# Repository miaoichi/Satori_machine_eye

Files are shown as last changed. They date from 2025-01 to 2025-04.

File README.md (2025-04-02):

# 機械覺之瞳

## 本專案基於 GPL3.0 開源協議，任何基於該專案的修改和衍生作品均需開源，且必須使用相同的 GPL3.0 協議！無良抄襲禁止！

## 作者
覺瞳模型：牧之原鈴華

攝影機瞳孔件：早睡（b站 鯊鯊製造）

PCB板：R餅銳度不夠

軟體：Cirnocon

fumo辨識：Yuan xu

覺之瞳計畫交流群 qq：727559409

## 專案結構
- `3d` 覺瞳模型文件

- `esp32eye` 覺瞳軟體

- `pcb` 覺瞳 ***pcb*** 板文件

- `LICENSE.txt` 開源協議

- `README.md`

## 食用方法

克隆此項目到本地，查看每個資料夾下的 ***README.md***

3d列印就查看 ***3d*** 資料夾，電路板查看 ***pcb***資料夾，軟體部分查看 ***esp32eye*** 資料夾。

連接覺之瞳 ***WiFi***：覺之瞳（無密碼）

瀏覽器開啟網頁遙控器：http://192.168.4.1

## 注意事項
電腦端滑鼠滾輪單獨控制上眼皮

手機遙控目前不太穩定，視訊推流畫質也不能再高了，主要是 ***esp32*** 算力和 ***AsyncWebServer*** 庫的限制，不建議視頻推流和遙控同時開啟，覺瞳被設置為奔潰自動閉眼並重啟。電腦端沒啥大問題。未來可能會用 ***vue3*** 重寫。

網頁頁面寫得不是很優雅，主要是我不會寫 ***css***，願意的話可以幫我改（（

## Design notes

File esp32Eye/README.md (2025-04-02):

# 機械覺之瞳-esp32eye
## 作者
Cirnocon -> miaoichi 

## 聯絡方式
電子郵件：miaoichi@gmail.com

GitHub：https://github.com/miaoichi

## 專案結構
- `ESP32EYE/`
 - `boards` 開發板設定文件，主要是啟用psram

 - `data` SPIFFS檔案儲存資料夾
 - `index.html` html文件

 - `nipplejs.min.js` 搖桿庫

 - `lib/` 自訂庫資料夾
 - `AsyncWebCam`

 - `src/` 原始碼資料夾
 - `main.cpp`

 - `partitions.csv` 分區表

 - `platformio.ini` ***PlatformIO*** 設定檔

## 食用方法
***vscode*** 下載 ***PlatformIO IDE*** 插件

> ***左側欄拓展圖示*** -> ***搜尋 PlatformIO IDE*** -> ***安裝***

打開 ***esp32eye*** 資料夾

> ***左上角檔案*** -> ***開啟資料夾*** -> ***找到 esp32eye 資料夾***

上傳 ***SPIFFS*** 系統文件

> ***左側欄小螞蟻圖示*** -> ***Bulid Filesystem Image*** -> ***Program Size*** -> ***Upload Filesystem Image***

編譯並燒錄文件

> ***左側欄小螞蟻圖示*** -> ***Build*** -> ***Upload***

## 注意事項
所有設定檔都是基於 ***ESP32-S3-N16R8*** 寫的

***platformio*** 的程式燒錄並不會自動更新 ***SPIFFS*** 系統文件，需要手動更新

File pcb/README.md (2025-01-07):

# 机械觉之瞳-pcb
## 作者
R饼锐度不够

## 嘉立创开源网址
https://oshwhub.com/flanker-e/esp32s3-open-source-of-jue

## 注意事项
板子天线需要自己单独购买

> 仅供参考：ESP8266 ESP-WROOM-02U ESP32-WROOM-32U IPEX天线2.4G ESP32天线 https://item.taobao.com/item.htm?id=598789753202

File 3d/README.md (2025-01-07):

# 机械觉之瞳-3d
## 作者
觉之瞳模型文件：觉之瞳项目交流群 qq：727559409

ov2640摄像头件：早睡（b站 鲨鲨制造）

## 食用方法
### 如何打印
直接打印 ***'已摆盘好.3mf'*** 文件

不建议修改摆盘方式，因为有些零件（比如眼球转轴）需要竖着打印，不然装配起来就非常麻烦，逝量打磨警告

如果你打算使用摄像头的话，请额外打印 ***'ov2640摄像头件'*** 文件夹里的两个文件，并删除 ***'已摆盘好.3mf'*** 文件中的瞳孔件（如果你不在意多打印一个零件的话，可以不删）

### 购买零件
舵机: mg90s 180° 

螺丝: M3\*4 M3\*6 M2\*3 若干

杜邦线：公对母 公对公 母对母若干

摄像头: ov2640 无畸变68度 （不装摄像头可以不买）

### 如何安装
***STR-lite*** 文件夹里存放的是所有零件的模型文件。使用任意可以查看 ***.prt*** 文件的软件打开里面的 ***STR-lite.prt*** 文件。手动调整零件位置，查看内部结构，然后拼装。

### 注意事项
不同材质打印的零件会有不同程度的膨胀或收缩，逝量打磨。

***STR-lite.prt*** 文件中名为 ***rack-lite*** 的零件与上眼皮的连接是要用502粘的

螺丝可以直接用买舵机送的螺丝（你甚至可以不拧，因为零件大概率会很紧）

购买舵机的时候请注意，是180度旋转范围的，不是90也不是360！90度的范围太小，360的不能控制旋转角度！

舵机建议购买tiankongrc品牌的。

摄像头瞳孔件是按照 ***ov2640 无畸变68度*** 设计的，即使型号一样，不同度数的摄像头大小也不一样！不要买错型号！（能安进去就当我没说，不过我没试过别的型号）

安装的时候请温柔，小心断件（（

记得上润滑油/雪油，转动更加丝滑

如果你打算把某些零件粘起来，请先调整好舵机角度！

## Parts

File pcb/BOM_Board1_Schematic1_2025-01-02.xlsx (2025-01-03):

No. | Quantity | Comment | Designator | Footprint | Value | Manufacturer Part | Manufacturer | Supplier Part | Supplier
1 | 9 | 100nF | C1,C29,C32,C33,C34,C35,C36,C37,C38 | C0603 | 100nF | CL10B104KB8NNNC | SAMSUNG(三星) | C1591 | LCSC
2 | 1 | 1uF | C2 | C0603 | 1uF | CL10A105KB8NNNC | SAMSUNG(三星) | C15849 | LCSC
3 | 7 | 10u | C4,C5,C26,C39,C40,C41,C42 | C0603 | 10u
4 | 8 | 22uF | C6,C7,C8,C9,C10,C11,C30,C31 | C0805 | 22uF | CL21A226MAQNNNE | SAMSUNG(三星) | C45783 | LCSC
5 | 1 | 2.2uF | C12 | C0603 | 2.2uF | CL10A225KB8NNNC | SAMSUNG(三星) | C913904 | LCSC
6 | 1 | 4.7uF | C13 | C0603 | 4.7uF | CL10A475KO8NNNC | SAMSUNG(三星) | C19666 | LCSC
7 | 3 | 220uF | C14,C15,C16 | CAP-SMD_BD6.3-L6.6-W6.6-FD-A | 220uF | OVZ221M0JTR-0606 | lelon(立隆) | C182403 | LCSC
8 | 2 | SS14L | D1,D2 | SOD-123F_L2.8-W1.8-LS3.7-RD |  | SS14L | Hottech(合科泰) | C190475 | LCSC
9 | 1 | 12H1300C | F1 | F1206 |  | 12H1300C | LANSON(良胜) | C182445 | LCSC
10 | 1 | AFC01-S08FCA-00 | FPC2 | FPC-SMD_P0.50-8P_FGS-XJ-H2.0 |  | AFC01-S08FCA-00 | JS(钜硕电子) | C262657 | LCSC
11 | 1 | AFC24-S24FIA-00 | FPC3 | FPC-SMD_P0.50-24P_QCHF-SM-H2.0 |  | AFC24-S24FIA-00 | JS(钜硕电子) | C262683 | LCSC
12 | 4 | HDR-M_2.54_1x3P | H1,H2,H3,H4 | HDR-TH_3P-P2.54-V-M |  |  |  | C2937625
13 | 1 | 1uH | L1 | IND-SMD_L7.0-W6.6 | 1uH | FXL0630-1R0-M | cjiang(长江微电) | C167216 | LCSC
14 | 1 | 4.7uH | L2 | IND-SMD_L4.4-W4.2 | 4.7uH | FXL0420-4R7-M | cjiang(长江微电) | C167208 | LCSC
15 | 4 | NCD0603Y1 | LED1,LED2,LED3,LED4 | LED0603-RD |  | NCD0603Y1 | 国星光电 | C84268 | LCSC
16 | 2 | SS8050_C541705 | Q1,Q2 | SOT-23-3_L2.9-W1.3-P1.90-LS2.4-BR |  | SS8050 | AnBon | C541705 | LCSC
17 | 8 | 10K | R7,R8,R9,R10,R16,R17,R18,R19 | R0603 | 10K
18 | 2 | 5.1K | R11,R12 | R0603 | 5.1K
19 | 1 | 500mΩ | R13 | R0805 | 500mΩ | FRL0805JR500TS | FOJAN(富捷) | C2934281 | LCSC
20 | 1 | 2 | R14 | R0603 | 2
21 | 1 | 100 | R15 | R0603 | 100
22 | 1 | 0 | R20 | R0603 | 0
23 | 1 | ESP32-S3-WROOM-1U-N16R8 | U2 | WIRELM-SMD_ESP32-S3-WROOM-1U |  | ESP32-S3-WROOM-1U-N16R8 | ESPRESSIF(乐鑫) | C3013946 | LCSC
24 | 1 | IP3005A | U3 | ESOP-8_L4.9-W3.9-P1.27-LS6.0-BL-EP |  | IP3005A | INJOINIC(英集芯) | C181685 | LCSC
25 | 1 | IP5306 | U4 | ESOP-8_L4.9-W3.9-P1.27-LS6.0-BL-EP |  | IP5306 | INJOINIC(英集芯) | C181692 | LCSC
26 | 1 | HC-C5080-2AS | U5 | CONN-TH_HC-C5080-2AS |  | HC-C5080-2AS | HCTL(华灿天禄) | C5221225 | LCSC
27 | 1 | AP63203WU-7 | U8 | TSOT-26_L2.9-W1.6-P0.95-LS2.8-BL |  | AP63203WU-7 | DIODES(美台) | C780769 | LCSC
28 | 1 | KH-SS12F23-G6 | U10 | SW-TH_KH-SS12F23-G6 |  | KH-SS12F23-G6 | kinghelm(金航标) | C5274466 | LCSC
29 | 1 | XC6206P282MR | U11 | SOT-23-3_L2.9-W1.3-P0.95-LS2.4-BR |  | XC6206P282MR | HXY MOSFET(华轩阳电子) | C5148690 | LCSC
30 | 1 | XC6206P182MR(1uA) | U12 | SOT-23-3_L2.9-W1.6-P1.90-LS2.8-BR |  | XC6206P182MR(1uA) | TECH PUBLIC(台舟) | C2827651 | LCSC
31 | 1 | CH340C | U13 | SOP-16_L10.0-W3.9-P1.27-LS6.0-BL |  | CH340C | WCH(南京沁恒) | C84681 | LCSC
32 | 1 | KH-TYPE-C-16P | USB1 | USB-C-SMD_KH-TYPE-C-16P |  | KH-TYPE-C-16P | Shenzhen Kinghelm Elec | C709357 | LCSC

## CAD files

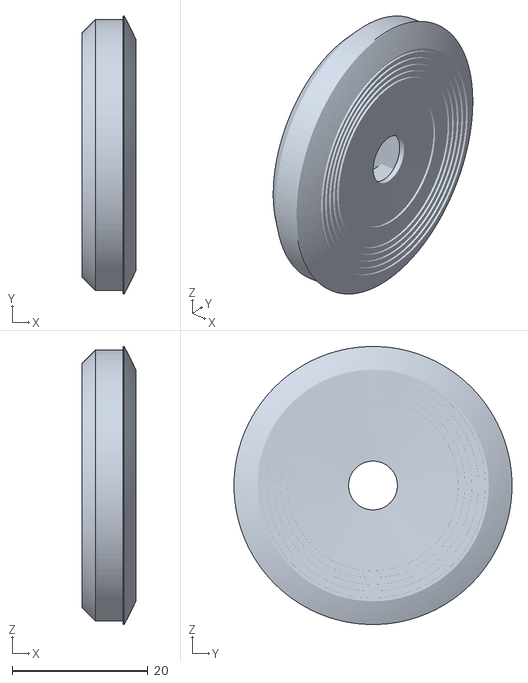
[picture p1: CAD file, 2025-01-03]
3d/ov2640摄像头件/瞳孔摄像头.stl
7.92 x 41.0 x 41.0

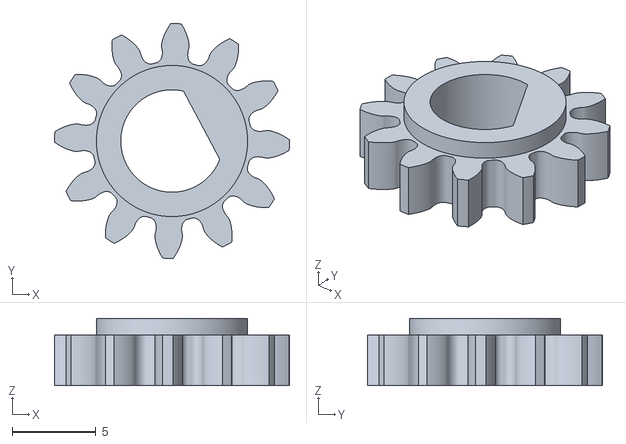
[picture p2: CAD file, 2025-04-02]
3d/stl/gear2.stl
14.0 x 14.0 x 4.00

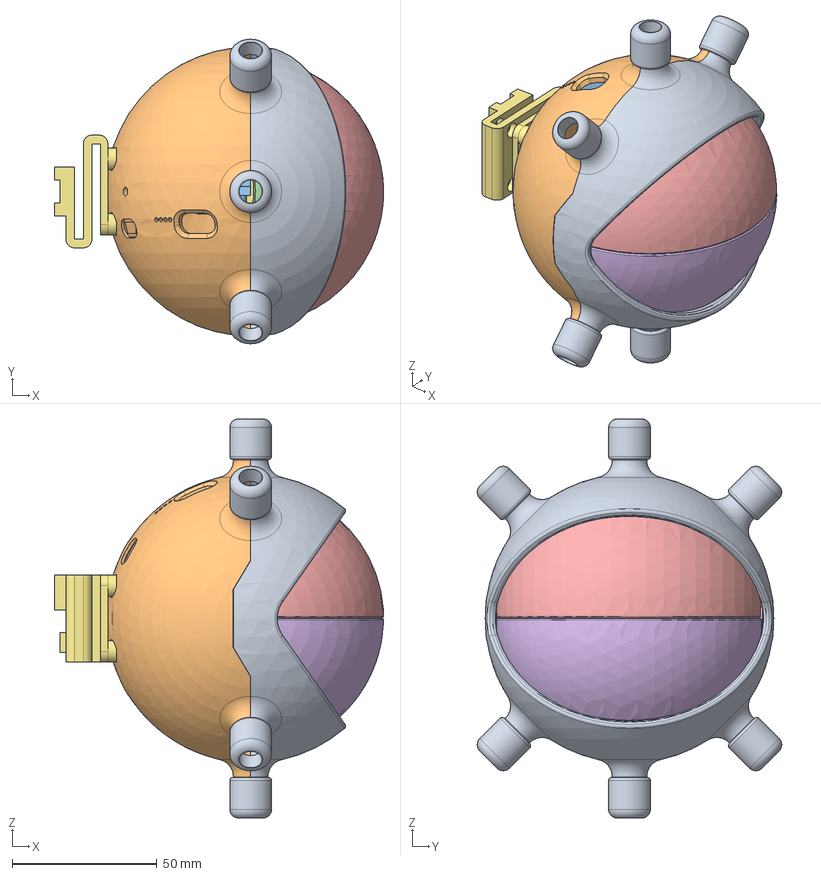
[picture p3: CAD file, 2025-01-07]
3d/STR-lite/step/STR-lite.stp
113.9 x 105.3 x 138.0 mm
MG90S x 3
servo pin
YAOBI
rocker
rack-lite
support-1
pupil
gear1
gear2

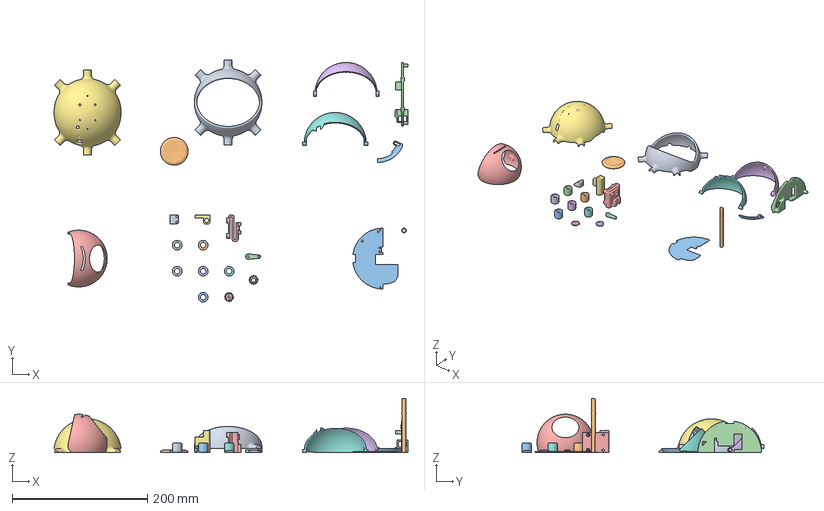
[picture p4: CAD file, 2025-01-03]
3d/已摆盘好.3mf
523.6 x 358.4 x 80.5 mm
01.stl
08.stl
pad.stl
03-1.stl
support-1.stl
06.stl
07.stl
05.stl
servo pin.stl
09.stl x 6
rack-rc.stl
04.stl
02.stl
pupil.stl
rocker.stl
gear1.stl
gear2.stl

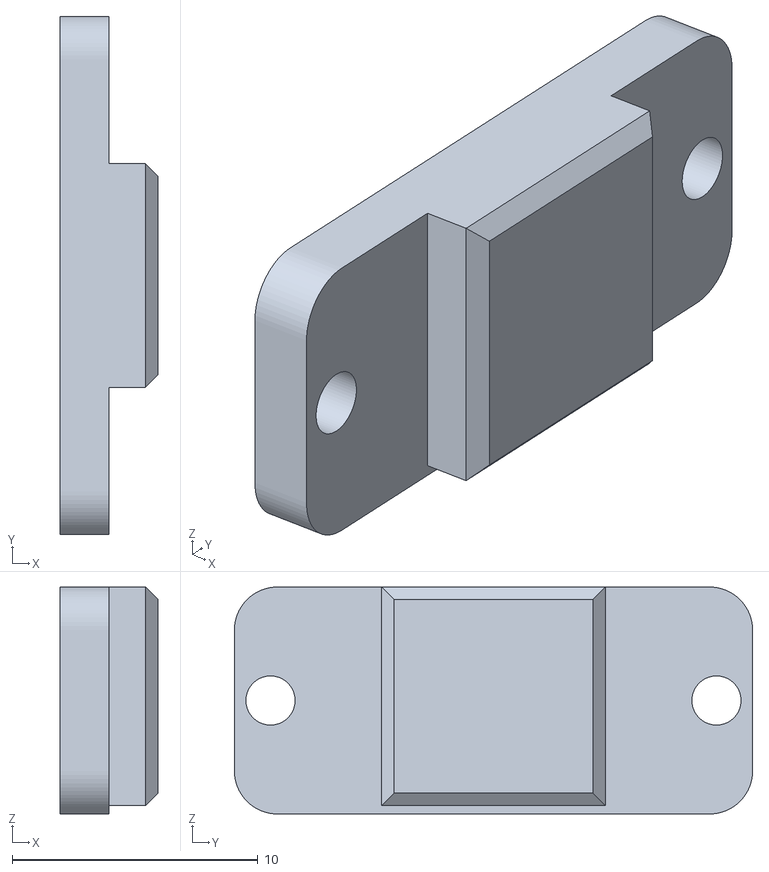
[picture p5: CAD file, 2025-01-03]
3d/ov2640摄像头件/瞳孔摄像头盖板.stl
4.00 x 21.1 x 9.24

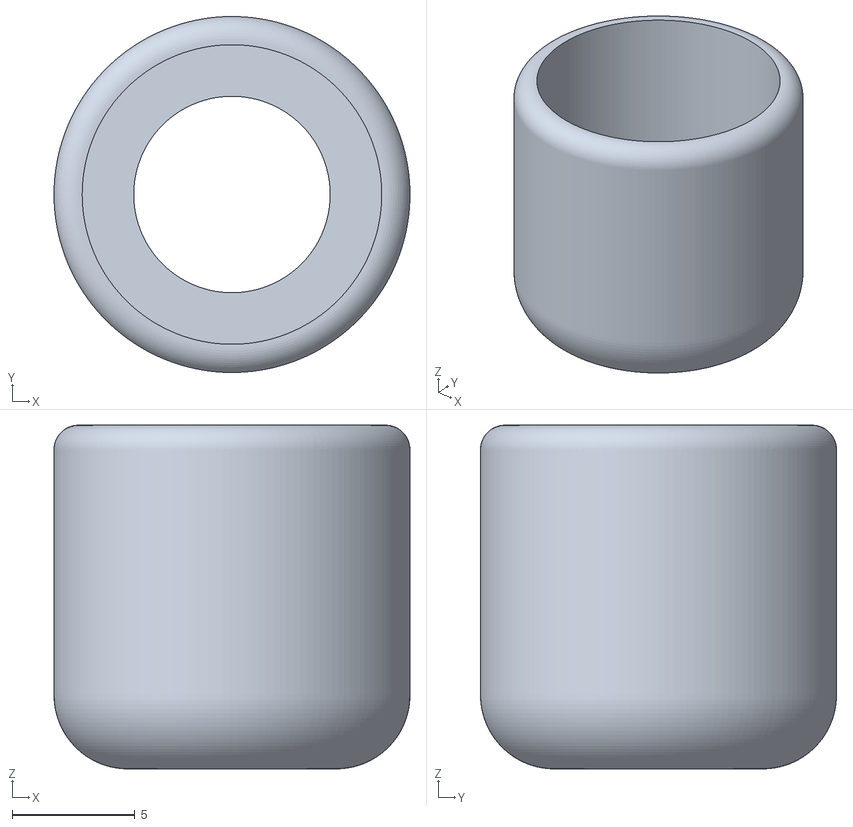
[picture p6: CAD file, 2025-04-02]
3d/stl/09.stl
14.5 x 14.5 x 14.0

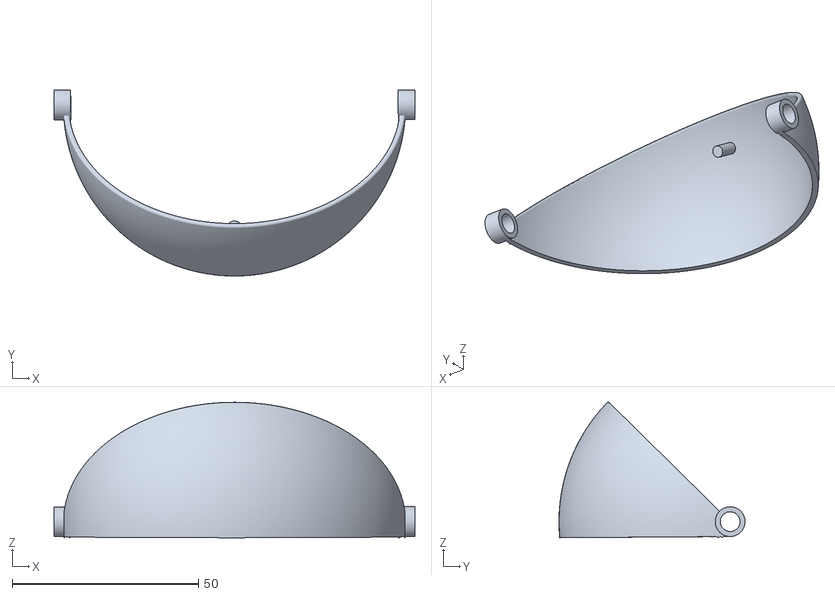
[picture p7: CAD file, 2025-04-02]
3d/stl/06.stl
97.0 x 50.0 x 36.4

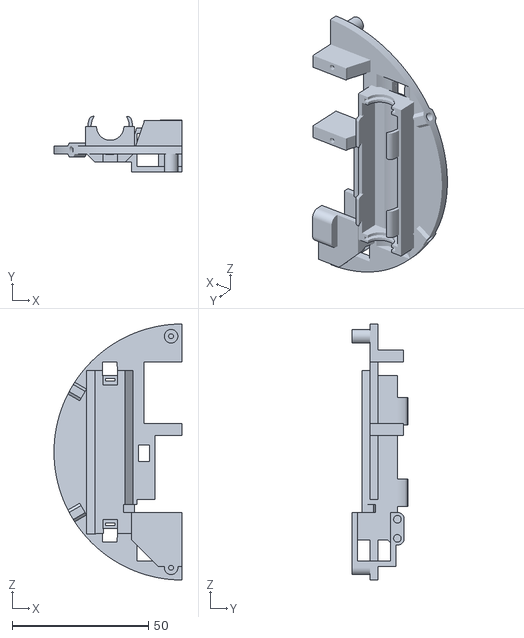
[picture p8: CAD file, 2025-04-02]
3d/stl/03-modfied1.stl.stl
47.0 x 20.4 x 94.0

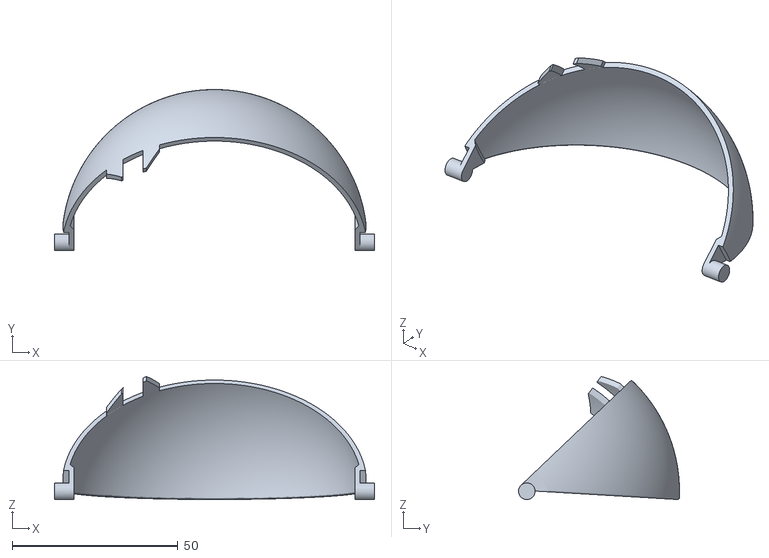
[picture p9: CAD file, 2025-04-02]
3d/stl/05.stl
96.4 x 48.5 x 37.1

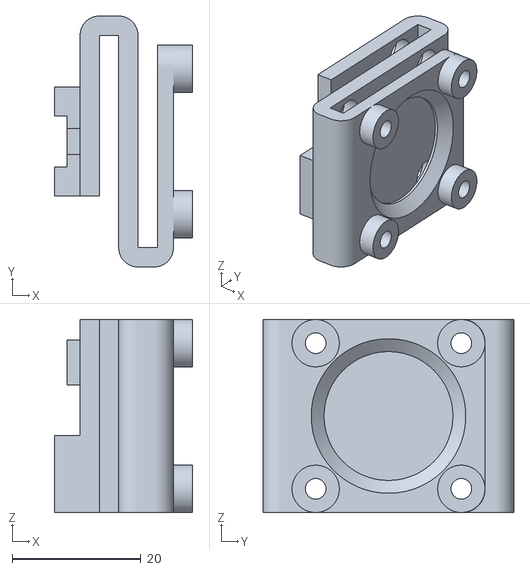
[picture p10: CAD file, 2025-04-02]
3d/stl/support-1.stl
21.5 x 39.0 x 30.0

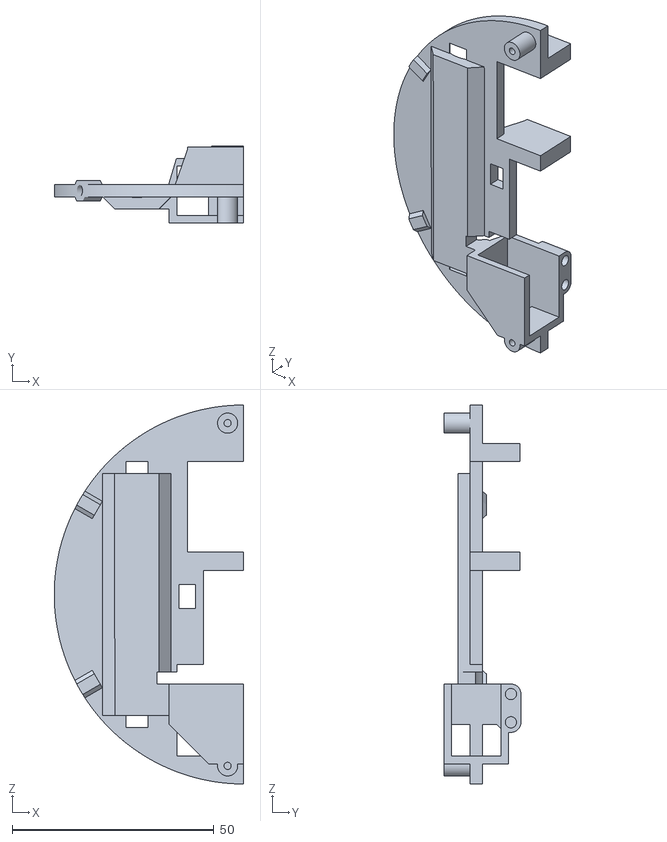
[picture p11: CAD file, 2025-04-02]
3d/stl/03-1.stl
47.0 x 19.1 x 94.0

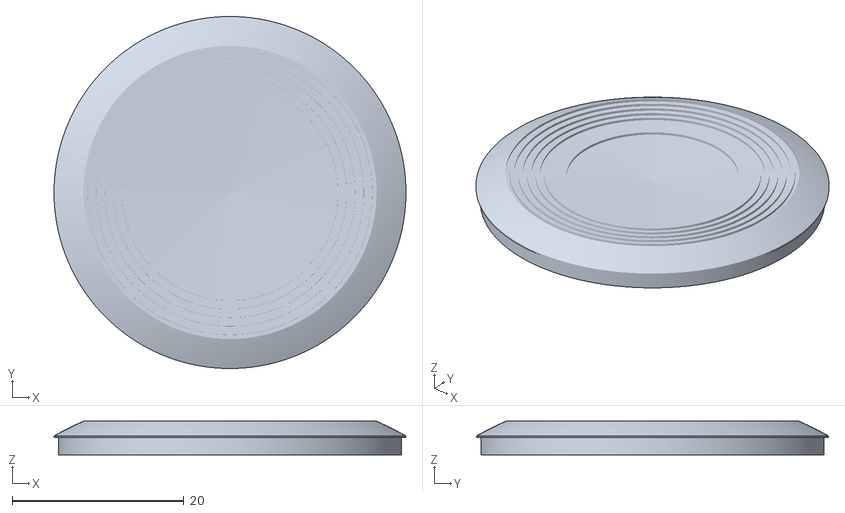
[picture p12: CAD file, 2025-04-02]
3d/stl/pupil.stl
41.0 x 41.0 x 3.92

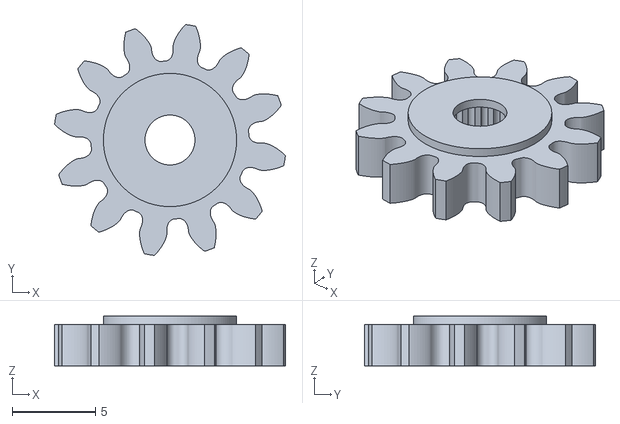
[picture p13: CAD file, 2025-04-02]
3d/stl/gear1.stl
13.9 x 13.9 x 3.00

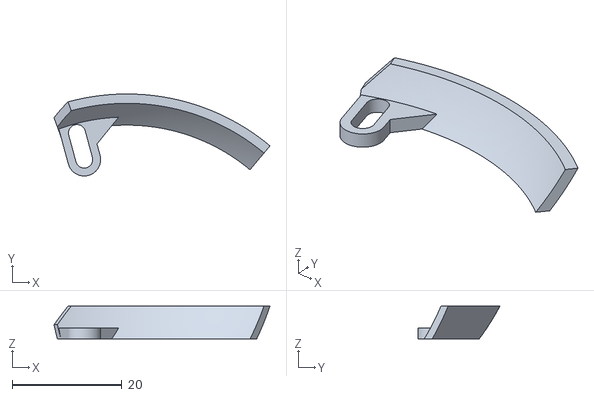
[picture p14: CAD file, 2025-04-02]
3d/stl/rack-lite.stl
39.4 x 15.0 x 6.00

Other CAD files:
3d/stl/servo pin.stl
3d/stl/07-modified.stl
3d/stl/08.stl
3d/stl/rocker.stl
3d/STR-lite/01.prt
3d/STR-lite/02.prt
3d/STR-lite/03-1.prt
3d/STR-lite/04.prt
3d/STR-lite/05.prt
3d/STR-lite/06.prt
3d/STR-lite/07.prt
3d/STR-lite/08.prt
3d/STR-lite/09.prt
3d/STR-lite/18650.prt
3d/STR-lite/MG90S.prt
3d/STR-lite/STR-lite.prt
3d/STR-lite/YAOBI.prt
3d/STR-lite/gear1.prt
3d/STR-lite/gear2.prt
3d/STR-lite/pupil.prt
3d/STR-lite/rack-lite.prt
3d/STR-lite/rocker.prt
3d/STR-lite/servo pin.prt
3d/STR-lite/support-1.prt
3d/stl/07.stl
3d/stl/09(1).stl
3d/stl/09(2).stl
3d/stl/09(3).stl
3d/stl/09(4).stl
3d/stl/09(5).stl
3d/stl/YAOBI.stl

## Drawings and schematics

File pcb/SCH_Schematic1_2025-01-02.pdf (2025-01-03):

### PW_USB5V

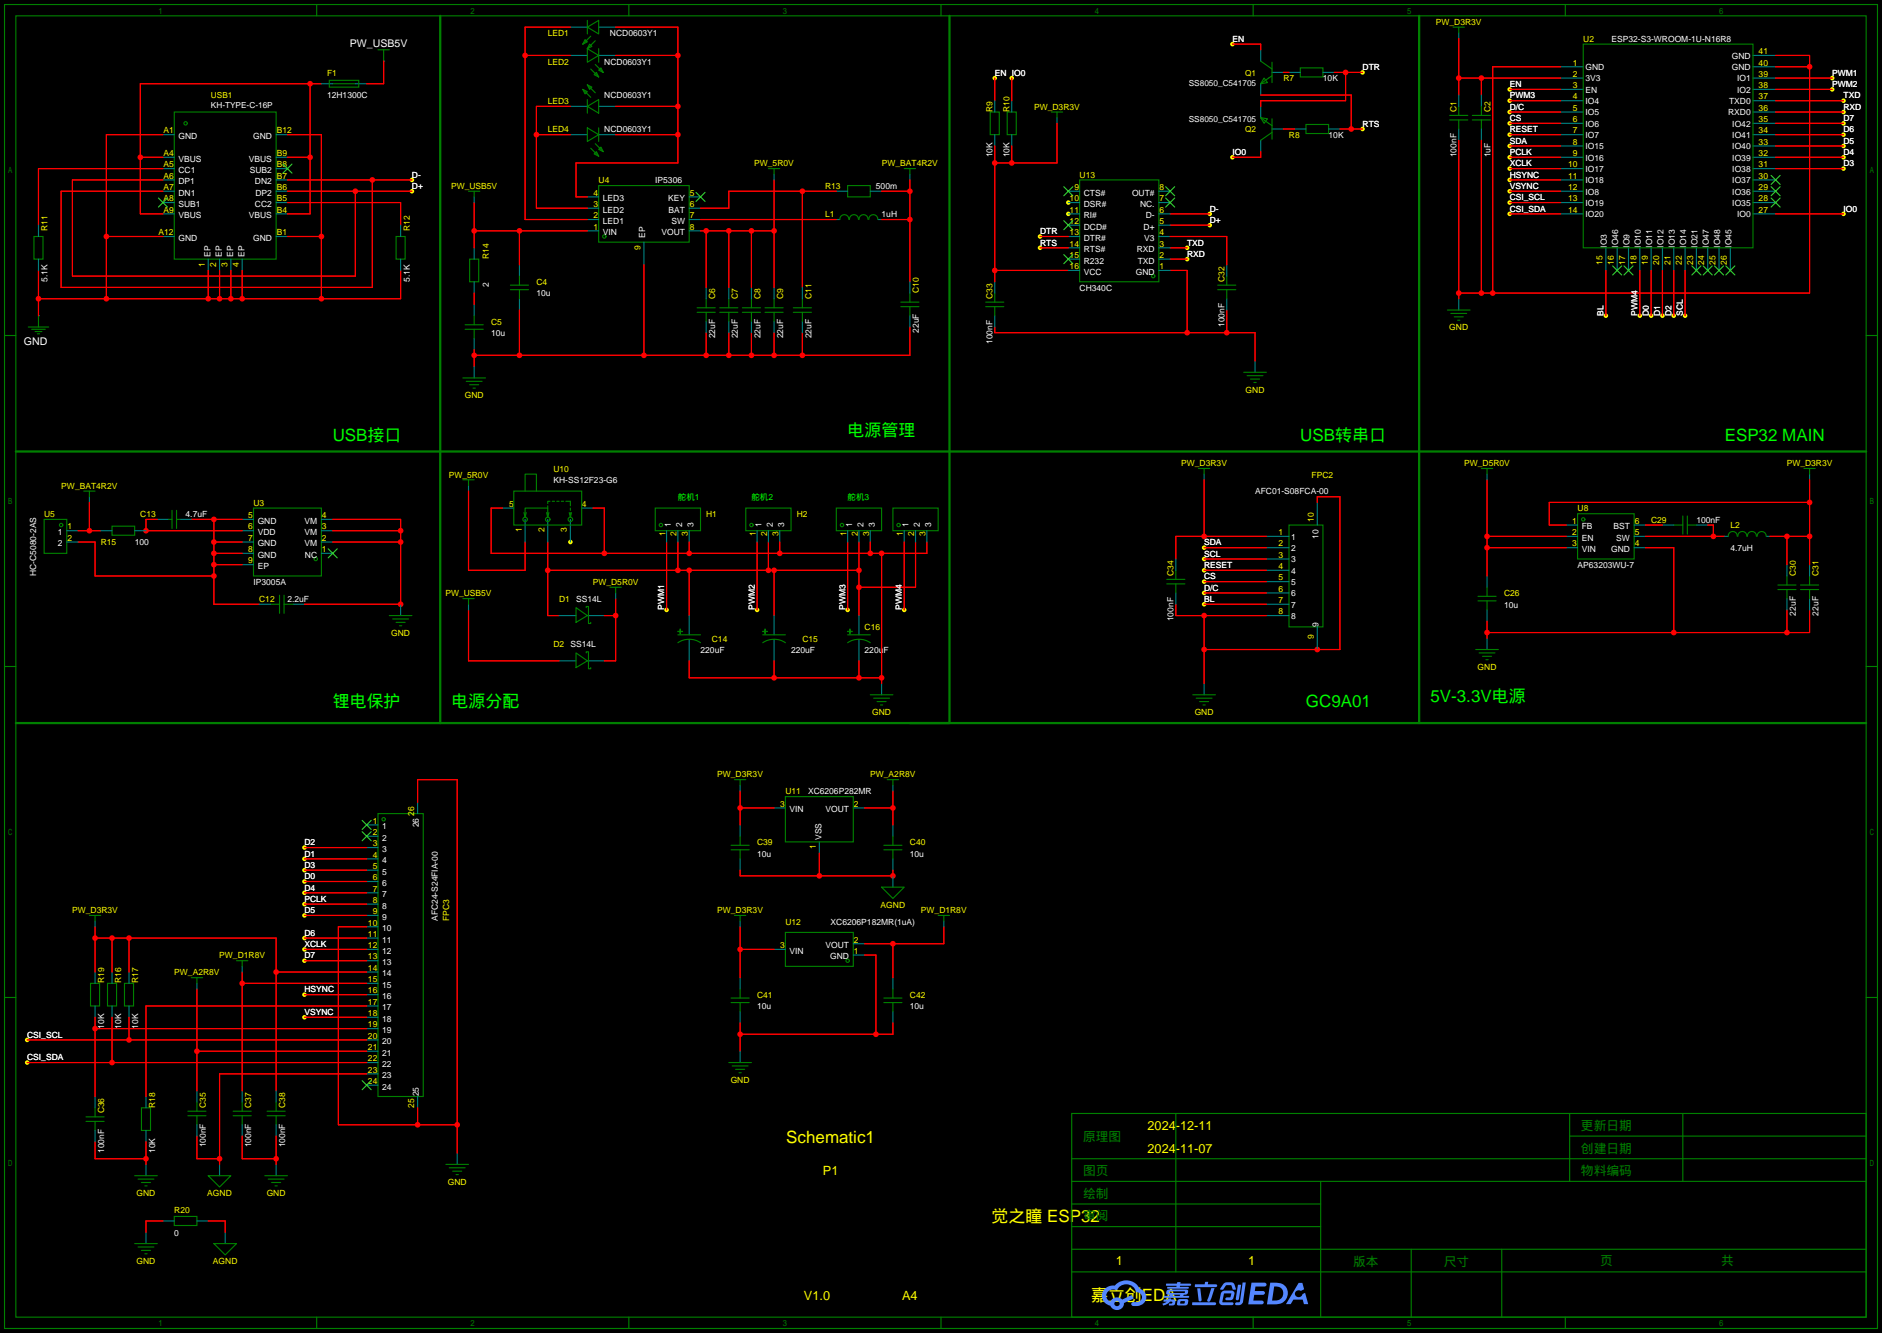
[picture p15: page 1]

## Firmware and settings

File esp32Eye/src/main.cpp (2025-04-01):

#include <AsyncWebCam.hpp>
#include <FaceDetect.hpp>
#include <ESP32Servo.h>

AsyncWebCam asyncwebcam;
FaceDetect facedetect;

Servo servoX, servoY, servoZ;
const int servoXPin = 1;
const int servoYPin = 2;
const int servoZPin = 4;

const struct { double min, max, def; } servoLimits[] = {
    {90, 170, 130}, {45, 100, 75}, {70, 170, 140}
};

Servo* servos[] = {&servoX, &servoY, &servoZ};


/* 參調用 */
const int TOTAL_STEPS = 150;      // 預設的最大步數
const int TOTAL_DELAY = 250; // 預設總時間（毫秒）

volatile float targetAngle[3] = {130, 45, 170};
volatile float currentAngle[3] = {130, 45, 170};

/* 三个舵機同時平滑轉動函數 */
void servo_smooth(float x, float y, float z) {
  int steps;
  float delaytime, maxAngleDiff, stepAngles[3], tA[3] = {x, y, z};

  // 判斷輸入值是否超出範圍
  if (tA[0] < servoLimits[0].min) tA[0] = servoLimits[0].min;
  if (tA[0] > servoLimits[0].max) tA[0] = servoLimits[0].max;
  if (tA[1] < servoLimits[1].min) tA[1] = servoLimits[1].min;
  if (tA[1] > servoLimits[1].max) tA[1] = servoLimits[1].max;
  if (tA[2] < servoLimits[2].min) tA[2] = servoLimits[2].min;
  if (tA[2] > servoLimits[2].max) tA[2] = servoLimits[2].max;

  // 計算最大角度差
  for (int i = 0; i < 3; i++) {
    float diff = abs(tA[i] - currentAngle[i]);
    if (diff > maxAngleDiff) maxAngleDiff = diff;
  }

  // 計算步數和每步延時
  steps = max(1, (int)(maxAngleDiff * TOTAL_STEPS / 180.0)); // 步數計算
  delaytime = TOTAL_DELAY / steps; // 每步延遲時間

  // 計算每步轉動角度
  for (int i = 0; i < 3; i++) {
    stepAngles[i] = (tA[i] - currentAngle[i]) / steps;
  }

  // 平滑地移動到目標角度
  for (int step = 0; step < steps; step++) {
    // 若有新資料立即中斷目前平滑過程
    if (asyncwebcam.newdata) break;
    
    // 否則更新currentAngle並寫入舵機
    for (int i = 0; i < 3; i++) {
      currentAngle[i] += stepAngles[i];
      servos[i] -> write(currentAngle[i]);
    }
    
    // 每步等待的時間
    delay(delaytime);
  }
}

void servo_smooth(float x, float y) {
  int steps;
  float z = y+65;
  float delaytime, maxAngleDiff, stepAngles[3], tA[3] = {x, y, z};

  // 判斷輸入值是否超出範圍
  if (tA[0] < servoLimits[0].min) tA[0] = servoLimits[0].min;
  if (tA[0] > servoLimits[0].max) tA[0] = servoLimits[0].max;
  if (tA[1] < servoLimits[1].min) tA[1] = servoLimits[1].min;
  if (tA[1] > servoLimits[1].max) tA[1] = servoLimits[1].max;
  if (tA[2] < servoLimits[2].min) tA[2] = servoLimits[2].min;
  if (tA[2] > servoLimits[2].max) tA[2] = servoLimits[2].max;

  // 計算最大角度差
  for (int i = 0; i < 3; i++) {
    float diff = abs(tA[i] - currentAngle[i]);
    if (diff > maxAngleDiff) maxAngleDiff = diff;
  }

  // 計算步數和每步延時
  steps = max(1, (int)(maxAngleDiff * TOTAL_STEPS / 180.0)); // 步數計算
  delaytime = TOTAL_DELAY / steps; // 每步延遲時

  // 計算每步轉動角度
  for (int i = 0; i < 3; i++) {
    stepAngles[i] = (tA[i] - currentAngle[i]) / steps;
  }

  // 平滑地移動到目標角度
  for (int step = 0; step < steps; step++) {
    // 若有新資料立即中斷目前平滑過程
    if (asyncwebcam.newdata) break;
    
    // 否則更新currentAngle並寫入舵機
    for (int i = 0; i < 3; i++) {
      currentAngle[i] += stepAngles[i];
      servos[i] -> write(currentAngle[i]);
    }
    
    // 每步等待的時間
    delay(delaytime);
  }
}


SemaphoreHandle_t Mutex;
bool is_mobile = false;
bool newdata = false;
int action;
float joystickX, joystickY, joystickZ;

TaskHandle_t servoTaskHandle; 
TaskHandle_t faceTracingTaskHandle; 

void faceTracingTask(void *pvParameters);

void servo_task(void *pvParameters) {
  Serial.println("Servo task on");  
  while (true) {
    if (xSemaphoreTake(Mutex, portMAX_DELAY) == pdTRUE) {
      if (asyncwebcam.newdata) {
        Serial.println("newdata");
        
        // 提取所有變數
        newdata = true;
        action = asyncwebcam.action;
        joystickX = asyncwebcam.joystickX;
        joystickY = asyncwebcam.joystickY;
        joystickZ = asyncwebcam.joystickZ;
        is_mobile = asyncwebcam.is_mobile;
        
        asyncwebcam.newdata = false;
      }
    }
    xSemaphoreGive(Mutex);
    

    if (newdata) {
      newdata = false;
      // 搖桿
      if (action == 0) {
        Serial.println("joystick");
        
        targetAngle[0] = servoLimits[0].def + joystickX * fabs(servoLimits[0].max - servoLimits[0].min);
        targetAngle[1] = servoLimits[1].def + joystickY * fabs(servoLimits[1].max - servoLimits[1].def);
        targetAngle[2] = joystickZ;
        
        if (is_mobile) {
          servo_smooth(targetAngle[0], targetAngle[1]);
        } else {
          servo_smooth(targetAngle[0], targetAngle[1], targetAngle[2]);
        }  
      }

      //人臉跟蹤
      else if (action == 1) {
        Serial.println("Servo task off, creating face tracing task"); 
        xTaskCreate(faceTracingTask, "FaceTracingTask", 32768, NULL, 1, &faceTracingTaskHandle);
        vTaskDelete(NULL); 
        
      }


      // 眨眼
      else if (action == -1) {
        Serial.println("activate action -1");

        double temp[2][2];
        temp[0][0] = servoLimits[1].min;
        temp[0][1] = servoLimits[2].max;// + fabs(currentAngle[0]-130) * 5 / 40;
        temp[1][0] = currentAngle[1];
        temp[1][1] = currentAngle[2];

        servo_smooth(currentAngle[0], temp[0][0], temp[0][1]);
        servo_smooth(currentAngle[0], temp[1][0], temp[1][1]);
        
        action = 0;
      }

      // 搖頭
      else if (action == -2) {
        Serial.println("activate action -2");

        double temp[3], xAdjustment=25; // 搖頭偏移量
        temp[0] = currentAngle[0]-xAdjustment;
        temp[1] = currentAngle[0]+xAdjustment;
        temp[2] = currentAngle[0];

        servo_smooth(temp[0], currentAngle[1], currentAngle[2]);
        servo_smooth(temp[1], currentAngle[1], currentAngle[2]);
        servo_smooth(temp[0], currentAngle[1], currentAngle[2]);
        servo_smooth(temp[2], currentAngle[1], currentAngle[2]);

        action = 0;
      }

      // 點頭
      else if (action == -3) {
        Serial.println("activate action -3");

        double temp[3], yAdjustment=25; // 點頭偏移量
        temp[0] = currentAngle[1]-yAdjustment;
        temp[1] = currentAngle[1]+yAdjustment;
        temp[2] = currentAngle[1];

        servo_smooth(currentAngle[0], temp[0], currentAngle[2]);
        servo_smooth(currentAngle[0], temp[1], currentAngle[2]);
        servo_smooth(currentAngle[0], temp[0], currentAngle[2]);
        servo_smooth(currentAngle[0], temp[2], currentAngle[2]);

        action = 0;  
      }

      // 閉眼
      else if (action == -4) {
        Serial.println("activate action -4");

        targetAngle[0] = servoLimits[0].def;
        targetAngle[1] = servoLimits[1].min;
        targetAngle[2] = servoLimits[2].max;
        servo_smooth(targetAngle[0], targetAngle[1], targetAngle[2]);

      }

      // 睁眼
      else if (action == -5) {
        Serial.println("activate action -5");

        targetAngle[0] = servoLimits[0].def;
        targetAngle[1] = servoLimits[1].def;
        targetAngle[2] = servoLimits[2].def;
        servo_smooth(targetAngle[0], targetAngle[1], targetAngle[2]);

      }  
    }
    vTaskDelay(pdMS_TO_TICKS(10));
  }
}

void faceTracingTask(void *pvParameters) {
  Serial.println("Face tracing task on");
  while (true) {
    if (xSemaphoreTake(Mutex, portMAX_DELAY) == pdTRUE) {
      if (asyncwebcam.newdata) {
      xSemaphoreGive(Mutex);
      Serial.println("Face tracking task off, creating servo task");
      xTaskCreate(servo_task, "ServoTask", 2048, NULL, 0, &servoTaskHandle);
      vTaskDelete(NULL);
      }
    }
    xSemaphoreGive(Mutex);
    
    Serial.println("!");
    
    facedetect.human_detect_position();

    vTaskDelay(pdMS_TO_TICKS(50));
  }
}


void setup() {
  Serial.begin(115200);
  // 初始化舵機
  servoX.attach(servoXPin);
  servoY.attach(servoYPin);
  servoZ.attach(servoZPin);  

  servoX.write(125);
  servoY.write(45);
  servoZ.write(170);
  
  asyncwebcam.start();
  Mutex = asyncwebcam.mutex;

  xTaskCreate(servo_task, "ServoTask", 2048, NULL, 0, NULL);

}


void loop() {  
  delay(1000);
}

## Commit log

2025-01-03 update files
    [01.prt, 01.stl, 02.prt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]
2025-01-06 重命名零件 网页摇杆修改
    [03-1.prt, axle.prt, back_cover.prt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]
2025-01-07 更新readme
2025-01-07 readme更新
2025-04-01 Build: Simplified Chinese to Traditional Chinese conversion
    - Converted all Simplified Chinese text to Traditional Chinese in the project.
    - Updated `esp32Eye/data/index.html` and `esp32Eye/src/main.cpp` with the changes.
2025-04-02 Update all stl files
    [03-1.stl, 03-modfied1.stl.stl, 05.stl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]
